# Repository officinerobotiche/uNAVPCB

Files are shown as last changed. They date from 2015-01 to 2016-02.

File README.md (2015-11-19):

# Officine Robotiche &micro;Nav PCB
**The first DC motor board in 4cm X 4cm** - PCB boards for &micro;Nav

This is a project in development by [Officine Robotiche] team, the check info at [official &micro;Nav site](http://unav.officinerobotiche.it/).

Feel free to ask for help, submit suggestions, satisfy your curiosity on our [**Users Group**](https://groups.google.com/forum/?hl=it#!forum/unav-users)

###Join on open firmware project [uNAV.X](https://github.com/officinerobotiche/uNAV.X)!!!

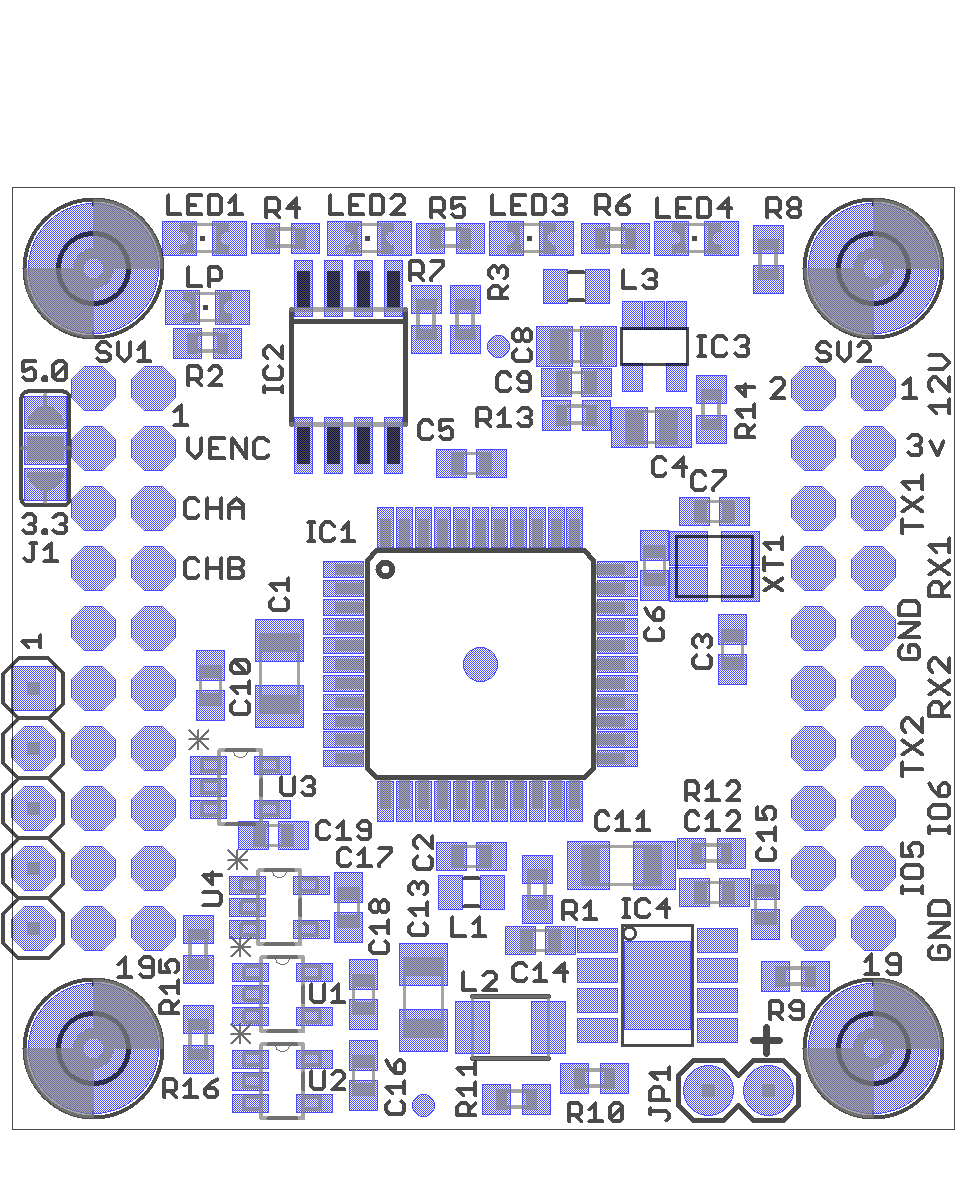
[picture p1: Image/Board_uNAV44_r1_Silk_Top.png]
uNAVPCB Silkscreen Top

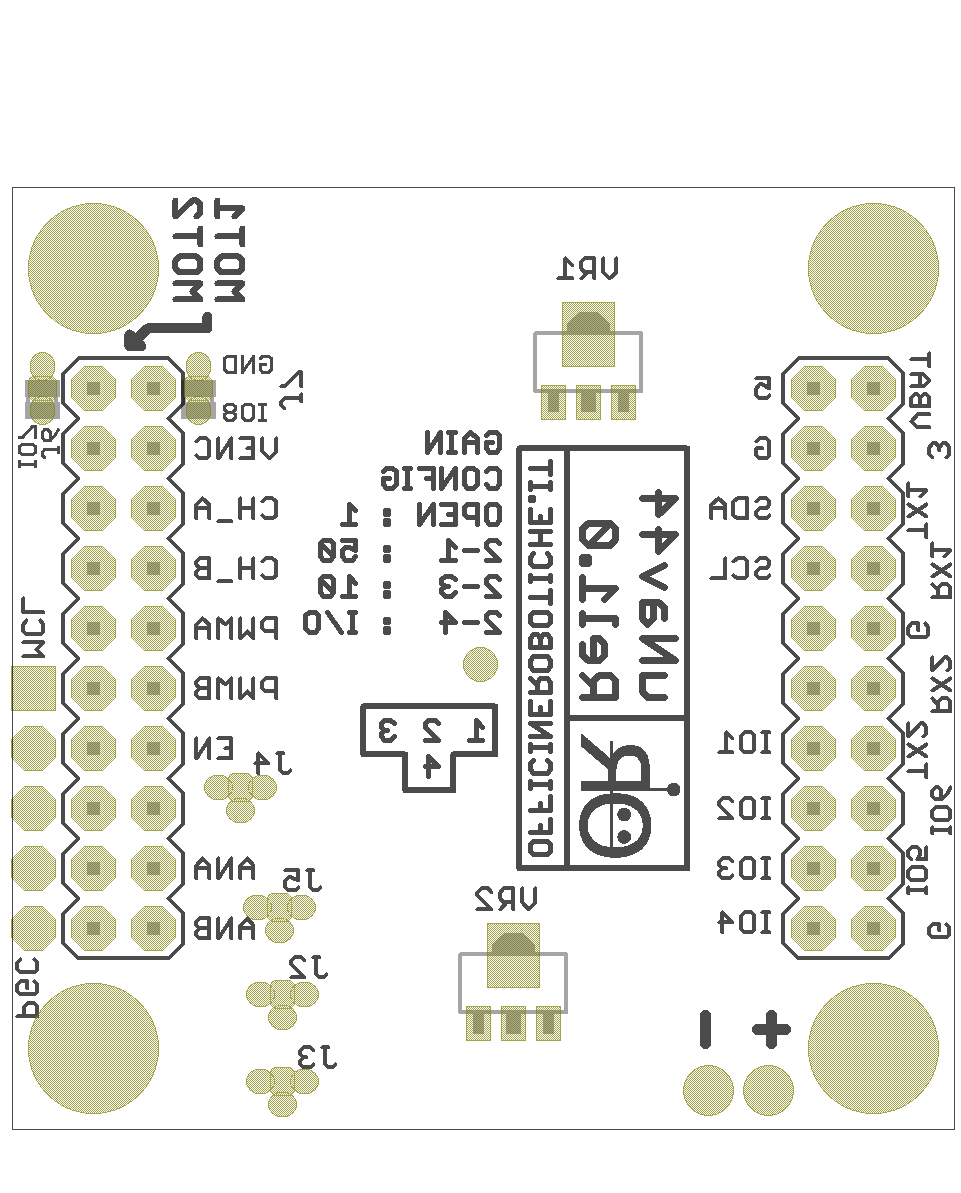
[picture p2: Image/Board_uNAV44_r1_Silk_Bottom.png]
uNAVPCB Silkscreen Bottom

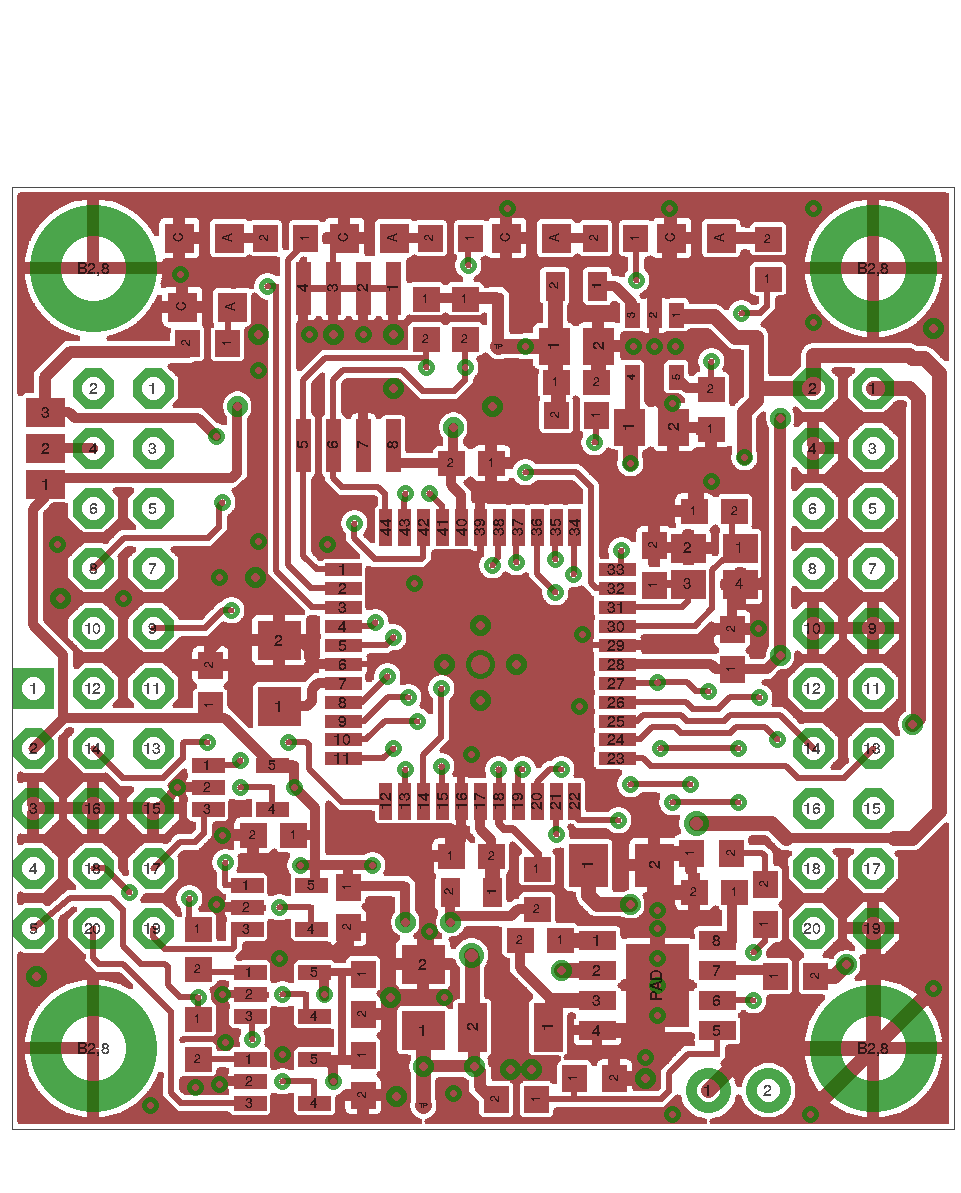
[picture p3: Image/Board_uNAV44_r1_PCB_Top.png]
uNAVPCB Silkscreen PCB Top

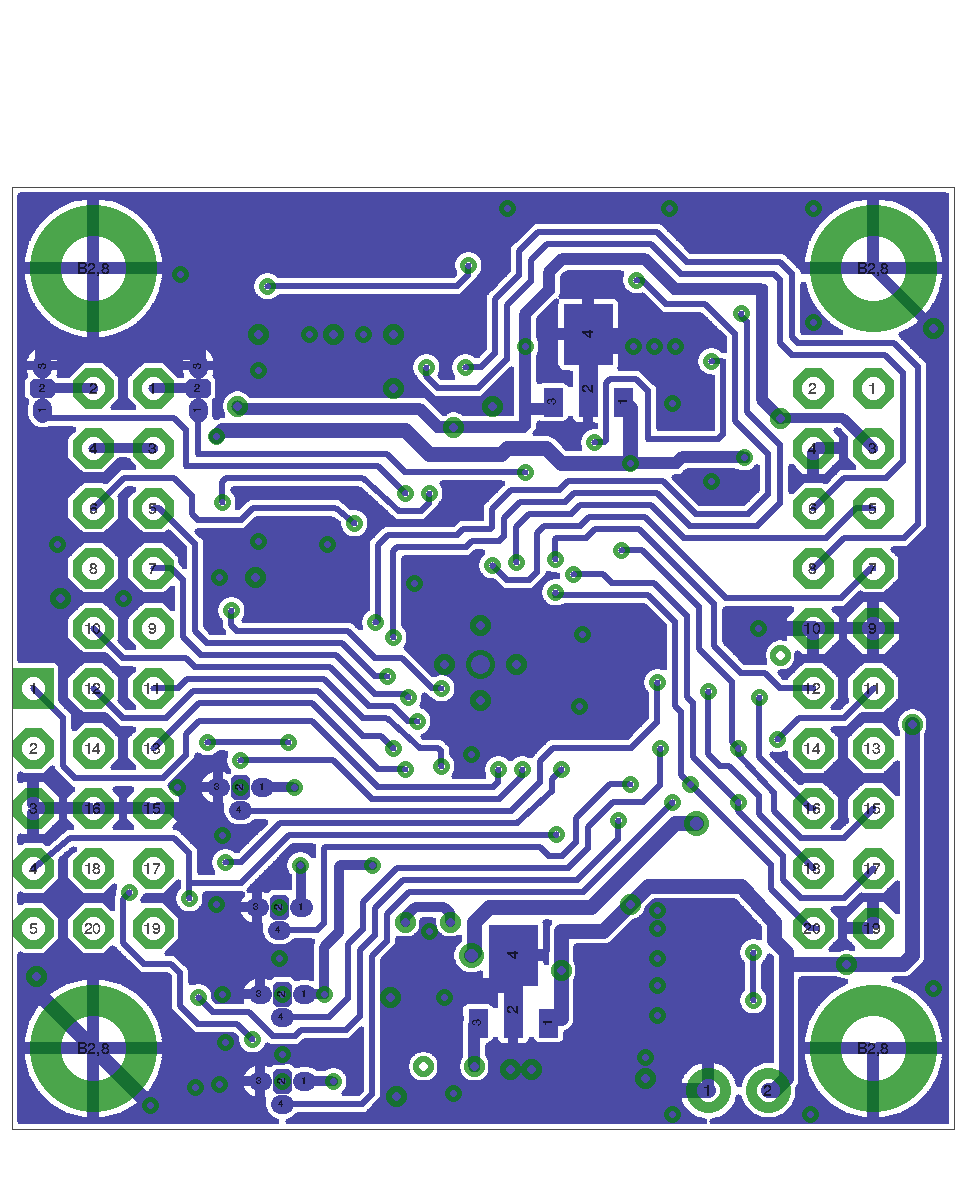
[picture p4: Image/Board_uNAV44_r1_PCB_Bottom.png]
uNAVPCB Silkscreen PCB Bottom


# Hardware features
- 2 DC motor control (external encoders and double H-bridge are required)
- size: 4cm x 4cm
- Matrix board with holes 2.54mm compliant
- Free 256Kb EEPROM in I2C 
- Voltage input *(Max 23V to 6V)*
- 2 internal regulators:
  - External input -> 5V
  - 5V -> 3.3V
- 4 LEDs
- ICSP programming

## DC Motor control
- 2 PWM outputs to control the speed of the motors
- Encoder input. *You can select 5V input or 3.3V to power on your encoders*: 
  - 2 channels (A, B)
  - 3 channels (A, B and Z axis)
- Analog input for current sensing
- Analog input for temperature sensing
- Pin to enable H-Bridge

## Communications
- 2 serial ports
- 1 I2C port
- 7 GP I/O (You can add feature remapping pins) 
 
# Available Shields
- [&micro;Bridge](https://github.com/officinerobotiche/uBridgePCB)

# Graphical tool for PID tuning
- [uNav_PID_Tuner](https://github.com/officinerobotiche/uNav_PID_Tuner)

[Officine Robotiche]:http://www.officinerobotiche.it/
[Logo]:http://2014.officinerobotiche.it/wp-content/uploads/sites/4/2014/09/ORlogoSimpleSmall.png

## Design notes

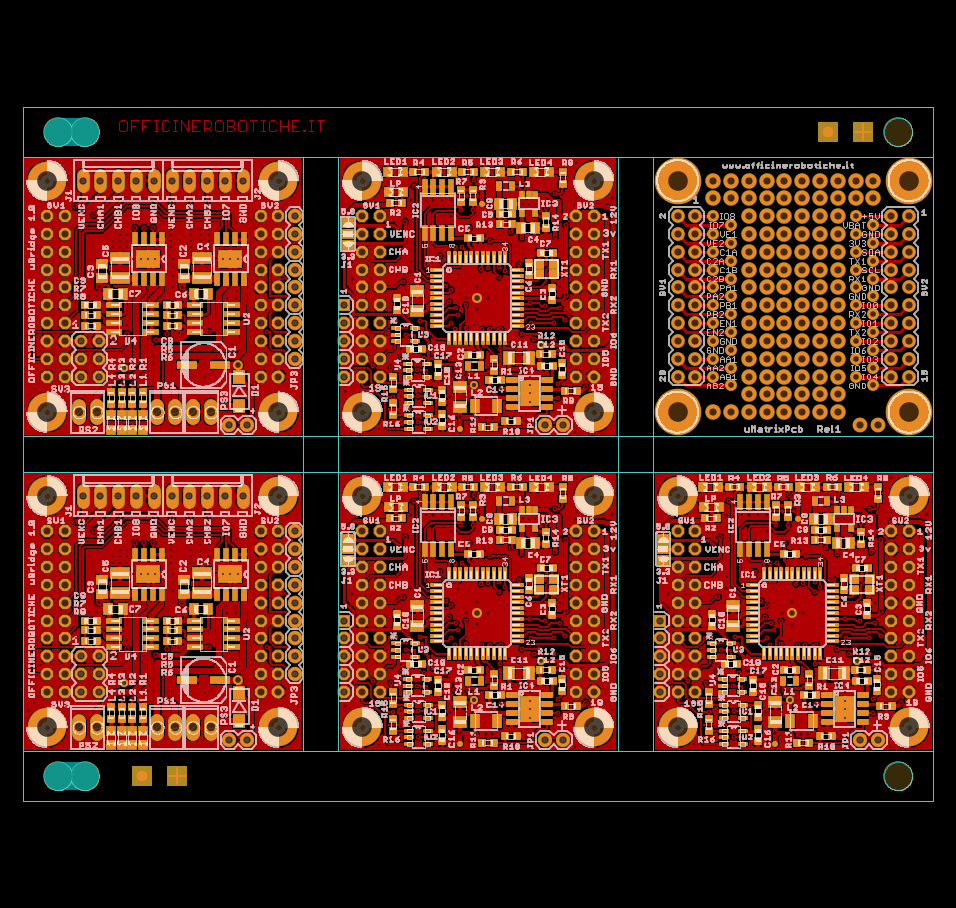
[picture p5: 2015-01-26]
Pannel/Image/Pannel_Top.png

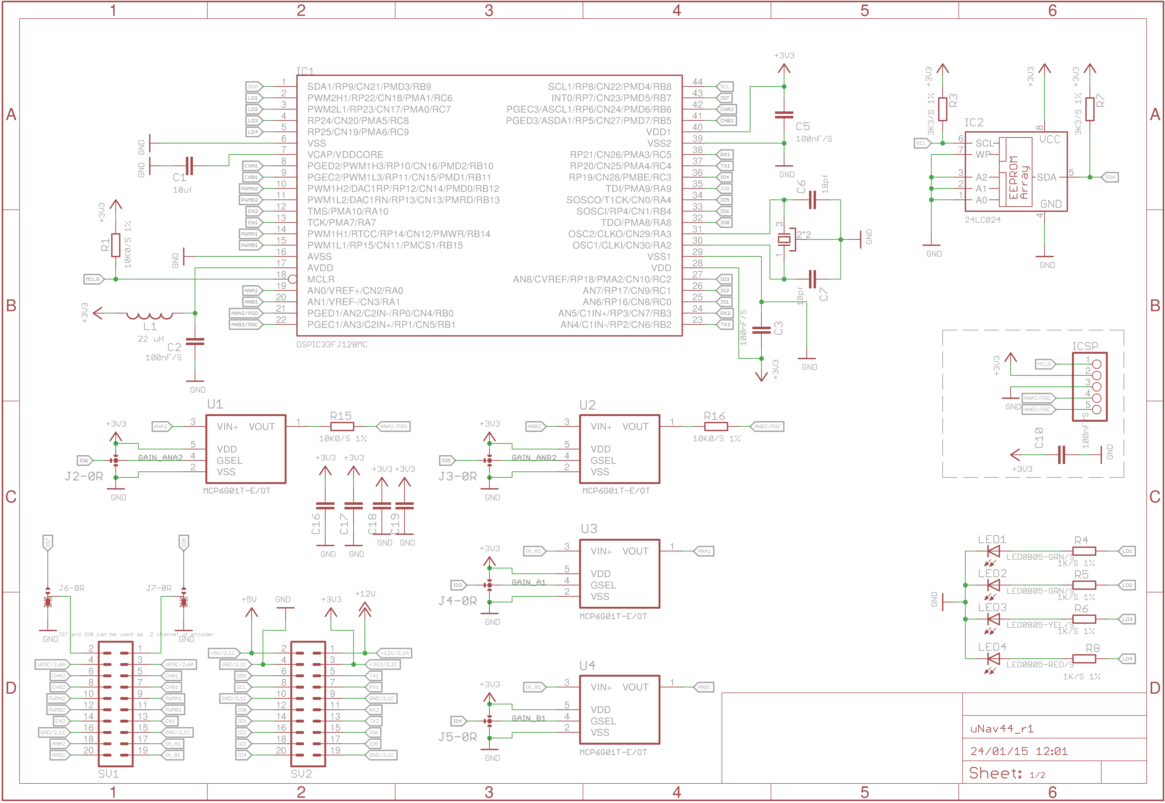
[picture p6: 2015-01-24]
Image/Scheme_uNAV44_r1_Sheet_1.png

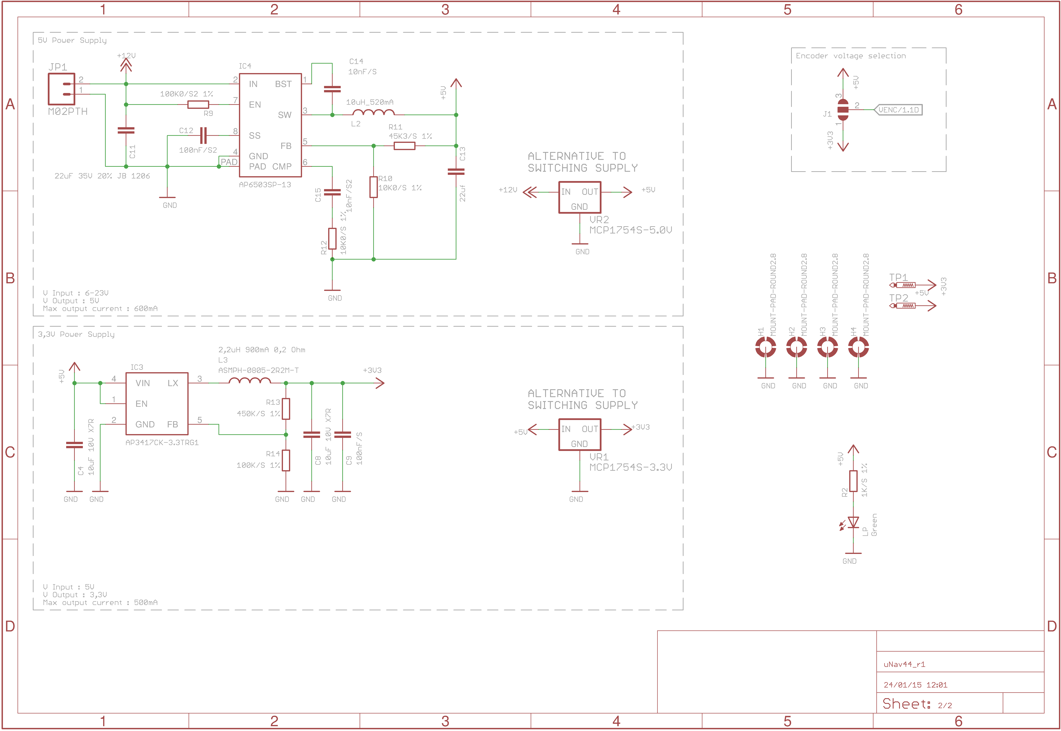
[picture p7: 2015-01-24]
Image/Scheme_uNAV44_r1_Sheet_2.png

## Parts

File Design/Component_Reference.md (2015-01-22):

#3V3 PSU
##AP3417CKTR-G1 : 0,3€
	- http://diodes.com/datasheets/AP3417C.pdf
	- http://www.digikey.it/product-detail/it/AP3417CKTR-G1/AP3417CKTR-G1DICT-ND/4505308
##2,2uH inductor : 0,26€
	-	http://www.abracon.com/Magnetics/power/ASMPH-0805.pdf
	- http://www.digikey.it/product-detail/it/ASMPH-0805-2R2M-T/535-12272-1-ND/4214872
##10uF 10V 20% X7R 0805 : 0,12€
	- http://www.digikey.it/product-detail/it/GRM21BR71A106MA73L/490-10517-1-ND/5026448

#For 6-23V to 5V PSU
##AP6503SP-13
	- http://www.diodes.com/datasheets/AP6503.pdf
	- http://www.digikey.it/product-detail/it/AP6503SP-13/AP6503SP-13DICT-ND/2767830
##22uF capacitor
	- CAP CER 22UF 35V 20% JB 0805 0,89€
	- http://www.digikey.it/product-detail/it/C2012JB1V226M125AC/445-11527-1-ND/3953193
	- CAP CER 22UF 35V 20% JB 1206 0,6€
	- http://www.digikey.it/product-detail/it/C3216JB1V226M160AC/445-11739-1-ND/3953405
##10µH Inductor 520mA/450mA 0806
	- http://www.yuden.co.jp/ut/product/category/inductor/BRC2016T100K.pdf
	- http://www.digikey.it/product-detail/it/BRC2016T100K/587-2177-1-ND/2002875

#Other new used components
##Xtal 10MHZ 8PF SMD: 0,55€
	- http://www.digikey.it/product-detail/it/7V-10.000MAAV-T/887-1791-1-ND/3586039
	- http://www.txccrystal.com/images/pdf/7v.pdf
##MCP6G01T-E/OT Selectable Gain Amplifier: 0,45€
- [DigiKey MCP6G01T-E/OTCT-ND]:http://www.digikey.com/product-detail/en/MCP6G01T-E%2FOT/MCP6G01T-E%2FOTCT-ND/1979730
- [DATASHEET of MCP6G01T-E/OT]:http://ww1.microchip.com/downloads/en/DeviceDoc/22004b.pdf

#Evaluated but discarded
##IC EEPROM 16KBIT 1MHZ SOT23-5 AT24C16D-STUM-T
- [DigiKey AT24C16D-STUM-TCT-ND]:http://www.digikey.it/product-detail/it/AT24C16D-STUM-T/AT24C16D-STUM-TCT-ND/5055821

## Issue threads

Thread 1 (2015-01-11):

Encoder connector in uBridge

rbonghi, 2015-01-11:
I would like to connect encoders in same uBridge board, this is possible?

I told with @Marnic @katodo on the meeting.

Marnic, 2015-01-11:
just added in sch file, @katodo now work on the board

rbonghi, 2015-01-12:
:+1:

katodo, 2015-01-12:
Ok, tomorrow I can check scheme...

katodo, 2015-01-20:
With jumper on I/O7 and I/O8  pin I can use this pin as GND for encoder attached directly on uNAV44.
This issue can be reopened on uBridge Repo.

Closed 2015-01-20.

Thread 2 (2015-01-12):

5 volt voltage regulator on board, why not?

bobboteck, 2015-01-12:
I saw that you have removed the 5Volt voltage regulator, this is not a choice that I like. Personally, I usually use a switching regulator Output 6.5 / 7.0V, this voltage reaches the various boards, where each has its voltage regulator for the required voltage. This, in my view, be also another benefit with regard to the cleaning of the supply signal, a cable that carries the 5V around for the robot is more subject to noise, and if used for direclty power a board, it can create problems.

Myzhar, 2015-01-12:
If you think to use the regulated 5V to power external encoders without the necessity to use other boards, I agree with you and I say that the uNav must have a 5V regulator onboard that generates that power voltage.

The only thing that makes me thinking is the power dissipation. Do we have enough space to place a power dissipator for the linear regulator?

@katodo @rbonghi @Marnic @guiott

katodo, 2015-01-12:
Have you statistic about encoder power consumption? there are a lot of
encoder type....
Can you also measure power supply current of uNav with software running?

Mauro Soligo by Sony Xperia Z
Il 12/gen/2015 16:32 "Walter Lucetti" <notifications@github.com> ha scritto:

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

katodo, 2015-01-12:
Ok, I've analyzed the problem and 5V are required! :)

Now, I can keep old solution with 2 LDO but I've found some better solution:
- http://www.analog.com/static/imported-files/data_sheets/ADP1864.pdf
- http://www.torex.co.jp/english/products/dcdc_converters/data/XC9503.pdf

First code can be powered with a supply up to 14V, second IC is dual-output and can be used for 3,3/5V out with a supply from 6 to 10V
They are a more expensive solution ( about 2€ Vs. <1€ of LDO version ) but is a very efficiency....

rbonghi, 2015-01-13:
I think second IC is more convenient to save space on PCB board and we don't use second layer to put ICs.

Finally I think is important to put a 5V regulator to power (in stand-alone version) the encoders.

katodo, 2015-01-13:
Price is 1,3€/each for 100pcs on digikey, with inductor and external mosfet solution can be expensive... now I search another IC...

katodo, 2015-01-13:
Another idea, a 2-stage supply:
Vin -> 5V with:
http://www.digikey.it/product-detail/it/AP6503SP-13/AP6503SP-13DICT-ND/2767830
Less than 0,7€ and up to 23V input

5V -> 3,3V with:
http://diodes.com/datasheets/AP3417C.pdf
http://www.digikey.it/product-detail/it/AP3417CKTR-G1/AP3417CKTR-G1DICT-ND/4505308
Less than 0,3€, without diode ( SYNCHRONOUS ) with a 2,2uH inductor ( @ 1,5Mhz ), can be the perfect solution for 3,3Vout in a space-save idea...

This is a complex but professional solution and no extremely expensive... with inductor and capacitor we are below 2,5€

@katodo @rbonghi @Marnic @guiott @bobboteck can be ok?

rbonghi, 2015-01-13:
ok! :+1:

bobboteck, 2015-01-13:
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

If there is enough space, for me is OK!!!

Marnic, 2015-01-13:
OK

katodo, 2015-01-20:
In final revision of scheme there are 2-stage switching reglator and optional LDO regulator... I consider closed this issue.

Closed 2015-01-20.

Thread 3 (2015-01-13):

Analog input analisys

katodo, 2015-01-13:
In uNav board there are 4 inputs reserved for analog operation.

In my idea all input must be "general porpouse" with a 0-3,3V input range and a medium high input impedance.

I've remove OA in board because pic input is also a "semi-general-porpouse" input and Operational Amplifier-related section is very conditioned by type of measure:

Measure of current in L'298 like shunt resistor require a gain depending by current and shunt resistor. For example with 2A on 0,1 Ohm resistor I need a gain of 16,5 to obtain 0-3,3 V range, but with a different driver driver like Allegro A4950 I need a 3,7 gain ( 3,5A and 0,25 Ohm resistor )... In this case OA section is not required and is only redundant.
In other bridge with hall-effect current sensor IC there are +/-5A +/-10A or bigger full-scale ( 2,5V @ 0A measure ) and a programmable OA can be required for a big accuracy on low current measure.
Also, a filter can be required...

Input for Voltage measure require a different section, I need a voltage divider and a filter depending by type of measured voltage ( input voltage, motor coil voltage etc... )

Besides, measure conditioning mus be near source of current/voltage under test... and in all case input section can't be equal and fixed...

guiott, 2015-01-13:
In the dsNav version of motor controller (see attached) there is an amplifier with a gain of 1 or 10 selectable by a soldering jumper. That's enough for a L298 h-bridge too, as I've used on Rino. Furthermore there is a minimal low-pass filter to filter out the PWM frequency. Further filtering is achieved via software procedures: using DMA of dsPIC33F ADC you can get 16 samples with no CPU intervention and compute the average after the interrupt trigger.
I agree at all that this can be redundant in many cases and the best solution is to condition the signal where it's generated, but this keep the board more general purpose.

On the other hand a simpler board, with less components, placed on the top layer only, costs less and results more attractive to most of the possible customers.

Is it possible to calculate the cost saving in the simpler solution? I think this is the best parameter to discuss on.

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

___________________
http://www.guiott.com/

katodo, 2015-01-13:
Ok, I'm evaluating this IC:
http://ww1.microchip.com/downloads/en/DeviceDoc/22004b.pdf
http://it.farnell.com/microchip/mcp6g01t-e-ot/amp-select-gain-single-1-mhz-smd/dp/1332148?ost=1332148

Gain is pin-selectable from 1, 10 and 50 value, IC is Rail-ToR-Rail and supplies is 1,8-5V range...
IC is small but I suspect that bottom side wil be needed and filer can't be perfomed in HW...
Voltage supply can be the same of dsPIC... ad will be the same...

During PCB update I will choose ideal version of IC ( 4pcs 1-channel or 1 IC at 4 ch ).
About 2 side version cost's, there are a lot of thing to be evaluated but in this stage I consider that, if there are some  IC on bottom side of PCB, they can be hand soldered.

@guiott @Marnic @Myzhar @rbonghi @bobboteck  can you "vote" this possible solution ( +1 or -1 )?

guiott, 2015-01-13:
Like!

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

___________________
http://www.guiott.com/ <http://www.guiott.com/>

Marnic, 2015-01-13:
OK
1++

Da: "Katodo" notifications@github.com
A: "officinerobotiche/uNAVPCB" uNAVPCB@noreply.github.com
Cc: "Marnic" marco@fabbrimarco.com
Data: Tue, 13 Jan 2015 01:14:45 -0800
Oggetto: Re: [uNAVPCB] Analog input analisys (#3)

> Ok, I'm evaluating this IC:

> http://ww1.microchip.com/downloads/en/DeviceDoc/22004b.pdf

> http://it.farnell.com/microchip/mcp6g01t-e-ot/amp-select-gain-single-1-mhz-smd/dp/1332148?ost=1332148

> Gain is pin-selectable from 1, 10 and 50 value, IC is Rail-ToR-Rail and supplies is 1,8-5V range...
>
IC is small but I suspect that bottom side wil be needed and filer can't be perfomed in HW...
>
Voltage supply can be the same of dsPIC... ad will be the same...

> During PCB update I will choose ideal version of IC ( 4pcs 1-channel or 1 IC at 4 ch ).
>
About 2 side version cost's, there are a lot of thing to be evaluated but in this stage I consider that, if there are some  IC on bottom side of PCB, they can be hand soldered.

> @guiott @Marnic @Myzhar @rbonghi @bobboteck  can you "vote" this possible solution ( +1 or -1 )?

> —
> Reply to this email directly or view it on GitHub.
>
  >

rbonghi, 2015-01-13:
:+1:

bobboteck, 2015-01-13:
+1

Myzhar, 2015-01-14:
+1

2015-01-13 16:28 GMT+01:00 Bobboteck <notifications@github.com>:

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

--
*Walter "Myzhar" Lucetti*

email myzhar@robot-home.it
web: *www.robot-home.it <http://www.robot-home.it/> - www.opencv.it
<http://www.opencv.it/>*
project:  http://myzharbot.robot-home.it

katodo, 2015-01-20:
in final revison of scheme I've added OA with configurable GAIN using MCU I/O... I consider closed this issue

Closed 2015-01-20.

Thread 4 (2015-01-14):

Component exchange for miniaturization

katodo, 2015-01-14:
can be exchanged this component?
- Actual 24AA01 EEPROM with this  AT24C16D-STUM-T 16Kbit in SOT23 case?
  http://www.digikey.it/product-detail/it/AT24C16D-STUM-T/AT24C16D-STUM-TCT-ND/5055821

- Actual 10Mhz xtal with this:
  http://www.digikey.it/product-detail/it/NX5032GA-10.000000MHZ-LN-CD-1/644-1033-1-ND/1128905

@rbonghi @guiott @Cyb3rn0id @Marnic @bobboteck

bobboteck, 2015-01-15:
I think there is no problem, you can talk to @guiott that developed the code to control the eeprom

katodo, 2015-01-15:
EEprom is last IC that can be changed but is a possibility.

Cordiali saluti
                        Mauro Soligo

Katodo  di Mauro Soligo
Via Molino Nuovo, 31 35012 Camposampiero PD Italy
P.IVA 04161520285  C.F. SLGMRA80L18B563Y
Cell: +39 3462137146  FAX: +39 0498591588  e-mail mauro.soligo@katodo.com

2015-01-15 12:16 GMT+01:00 Bobboteck <notifications@github.com>:

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

rbonghi, 2015-01-15:
I'm agree to increase free area space on unav pcb board. :+1:

katodo, 2015-01-19:
Only XTAL was changed.

Closed 2015-01-19.

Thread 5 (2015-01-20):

Move GND near TX2

bobboteck, 2015-01-20:
Is possible in the BUS connector, move the actual GND near IO5, near the TX2 pin, in place oh IO6?

Marnic, 2015-01-20:
you think to use two UART? if not, you can make just only one cable TX-RX-GND and if you rotate the cable 180 degrees you have GND-RX-TX so as displaced in the bus connector

katodo, 2015-01-20:
and, if you use 2 uart, you can use a single cable with a common GND...

Replace a I/O with GND isn't possible in this board, I'm sorry.

  Mauro

2015-01-20 11:06 GMT+01:00 Marnic <notifications@github.com>:

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

bobboteck, 2015-01-20:
@Marnic, Yes use two UART, if you want connect two uNav!

Ok if is not possible, as I said it's only a question "if is possible".

Closed 2015-01-20.

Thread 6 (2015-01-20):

Fourth mount pad

bobboteck, 2015-01-20:
I have see there is only 3 mount pad, but we have four hole. I see also there aren't enough sapce to put it. My question is, tis hole can't be used for mounting the board?

katodo, 2015-01-20:
3 pad have GND ring and fourth PAD is a simple hole, can be used for PCB fix but must be used with caution ( plastic screw or washer ). In final version I can check a solution...

katodo, 2015-01-22:
Added... solved :)

Closed 2015-01-22.

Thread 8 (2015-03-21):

Inversion of polarity destroy uNav

katodo, 2015-03-21:
uNav used without uBridge will be destroyed is inversion supply voltage occur.

A input diode can be usefull...

Myzhar, 2015-03-23:
Yeah! Protection anti-inversion is useful...
Il 21/Mar/2015 02:09 "Katodo" <notifications@github.com> ha scritto:

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

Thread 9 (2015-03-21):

Input inductor size

katodo, 2015-03-21:
A 15uH 1,2A 0.204 Ω in 4,5x4mm size is better inductor in input switching power supply.
In V1 PCB version can be soldered but in V2 pcb module bust be updated.

Ideal component is Wurth Elektronik code:  744773115

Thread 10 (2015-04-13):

C16 to C19 Capacitor size

gbr1, 2015-04-13:
C16 C17 C18 C19 capacitors size isn't specified

Myzhar, 2015-04-13:
The capacitors are 100nF

@katodo please add the information on the schematic as soon as you can

katodo, 2015-04-13:
ok, information in SCH file is hidden only  ( in 1.1.sch file). If you open file with Eagle vale can be read, in next days I try to update file on Git.

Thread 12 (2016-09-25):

Change PGED & PGEC lines

rbonghi, 2016-09-25:
At this time the PGED & PGEC lines are connected on pin 21 and 22. The same line of motor 1 current and voltage adc line.

I suggest to move in other place. In  PGED3 & PGEC3, in pin 41, 42 and move CHB1 and CHB2 in other remappable place.

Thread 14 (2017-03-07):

Discussion of board

Russ76, 2017-03-07:
Do you have somewhere posted a comprehensive discussion of what you are trying to accomplish with this project, and how this board(s) will be superior to other alternatives already on the market? Will it control large motors, like 25 amps? Is the ROS software available now for use of this board?

Myzhar, 2017-03-07:
@Russ76 you are putting good questions.

We are still trying to understand if "reinventing the wheel" is a good road to follow.

The starting idea was the one to create by ourself a tiny dual channels motor driver (4cm x 4cm)  with logic and power separated. This module (uNAVPCB) cannot directly drive any motor because it only generates two PWM signals to be sent to an external H-Bridge, controlling speed (dual channels QEI encoders are supported) and torque, if you can provide analog current sensing.

I can reply to the second of your question: YES, you can drive large motors, only if you use the right H-Bridge for that kind of motors. The uNAV can theoretically drive any kind of motor...

About ROS... yes, we have ROS drivers:  https://github.com/officinerobotiche/ros_orbus_interface
Here you can find the also the firmware for the board: https://github.com/officinerobotiche/uNAV.X

Now the reply to the first question... it is a phylosophical question because analizing the market I can say that there is not the needing for a new motor controller board. You can find a lot of good motor drivers on the market, with a good ROS support, RoboteQ's (e.g. SDC2160) and Ion Motion Control's (RoboClaws) are good examples. Sometimes the market must not be a limitation, a new project can also be a good way to make practice with hardware and to study new software algorithms.
To finish this long reply: if I need to go on the market with a new "robot" I will not create a new motor controller board, but I will use something available off the shelf to not waste time and money; if I want to make a bit of research in the field of motor control I will create my own board trying to understand what I can do better than other product on the market (i.e. speed and torque control on a dual PID loop).

I hope to have replied to all of your question, please let me know what you think about.

Walter

Russ76, 2017-03-07:
Thanks for that, Walter! Your board is very small, that is good. And I'm sure the research and project operation was educational for several of you. Building a robot at this time is an educational project and not easy; there is so much to learn. Just learning ROS itself is challenging.
For motor control I'm using a Sabertooth and Kangaroo. Just installed encoders last week. We'll see how it works. Please let us know when your uNav is market ready!

Myzhar, 2017-03-07:
@Russ76 Thank you

Closed 2017-03-16.

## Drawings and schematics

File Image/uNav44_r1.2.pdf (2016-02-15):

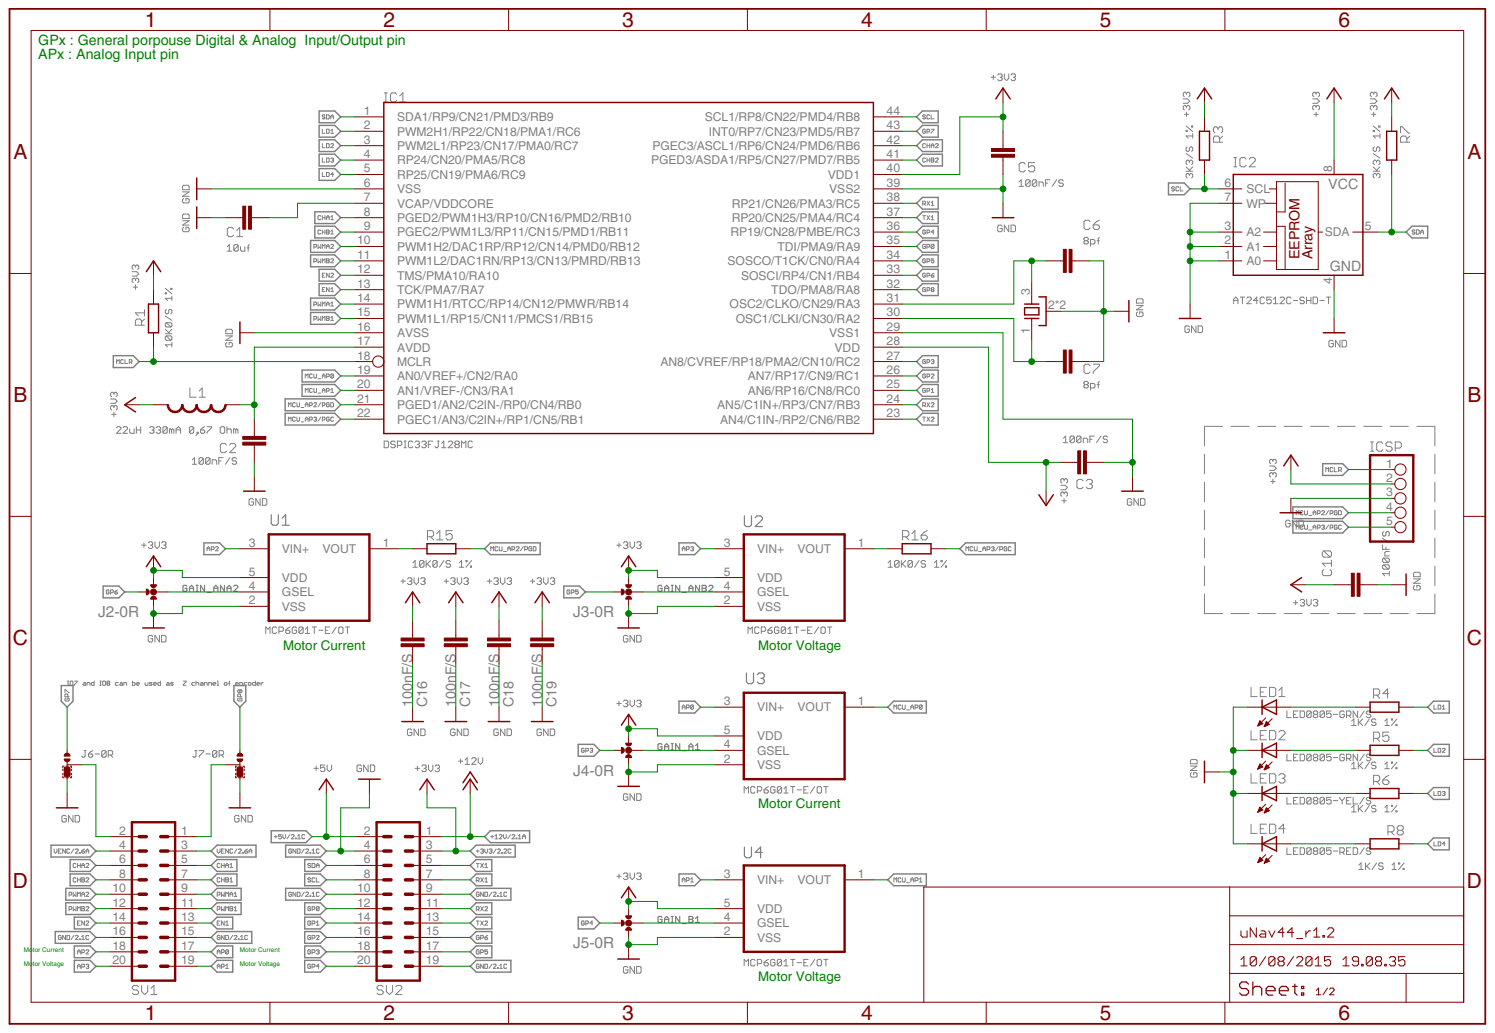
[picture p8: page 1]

100nF/S 100nF/S 100nF/S 100nF/S SDA1/RP9/CN21/PMD3/RB9 1 PWM2H1/RP22/CN18/PMA1/RC6 2 PWM2L1/RP23/CN17/PMA0/RC7 3 RP24/CN20/PMA5/RC8 4 RP25/CN19/PMA6/RC9 5 VSS 6 VCAP/VDDCORE 7 PGED2/PWM1H3/RP10/CN16/PMD2/RB10 8 PGEC2/PWM1L3/RP11/CN15/PMD1/RB11 9 PWM1H2/DAC1RP/RP12/CN14/PMD0/RB12 10 PWM1L2/DAC1RN/RP13/CN13/PMRD/RB13 11 TMS/PMA10/RA10 12 TCK/PMA7/RA7 13 PWM1H1/RTCC/RP14/CN12/PMWR/RB14 14 PWM1L1/RP15/CN11/PMCS1/RB15 15 AVSS 16 AVDD 17 MCLR 18 AN0/VREF+/CN2/RA0 19 AN1/VREF-/CN3/RA1 20 PGED1/AN2/C2IN-/RP0/CN4/RB0 21 PGEC1/AN3/C2IN+/RP1/CN5/RB1 22 AN4/C1IN-/RP2/CN6/RB2 23 AN5/C1IN+/RP3/CN7/RB3 24 AN6/RP16/CN8/RC0 25 AN7/RP17/CN9/RC1 26 AN8/CVREF/RP18/PMA2/CN10/RC2 27 VDD 28 VSS1 29 OSC1/CLKI/CN30/RA2 30 OSC2/CLKO/CN29/RA3 31 TDO/PMA8/RA8 32 SOSCI/RP4/CN1/RB4 33 SOSCO/T1CK/CN0/RA4 34 TDI/PMA9/RA9 35 RP19/CN28/PMBE/RC3 36 RP20/CN25/PMA4/RC4 37 RP21/CN26/PMA3/RC5 38 VSS2 39 VDD1 40 PGED3/ASDA1/RP5/CN27/PMD7/RB5 41 PGEC3/ASCL1/RP6/CN24/PMD6/RB6 42 INT0/RP7/CN23/PMD5/RB7 43 SCL1/RP8/CN22/PMD4/RB8 44 VCC GND 8 4 SCL 6 SDA 5 A0 1 A1 2 A2 3 WP 7 12345 135 246 79 810 111315 121416 1719 1820 135 246 79 810 111315 121416 1719 1820 1 3 2*2 C16 VIN+ 3 GSEL 4 VSS 2 VDD 5 VOUT 1 C17 VIN+ 3 GSEL 4 VSS 2 VDD 5 VOUT 1 VIN+ 3 GSEL 4 VSS 2 VDD 5 VOUT 1 VIN+ 3 GSEL 4 VSS 2 VDD 5 VOUT 1 C18 C19 J2-0R J3-0R J4-0R J5-0R ABCD 1 2 3 4 5 6 ABCD 1 2 3 4 5 6 Array EEPROM GPx : General porpouse Digital & Analog Input/Output pin APx : Analog Input pin Motor Current Motor Current Motor Voltage Motor Voltage Motor Voltage Motor Current Motor Voltage Motor Current

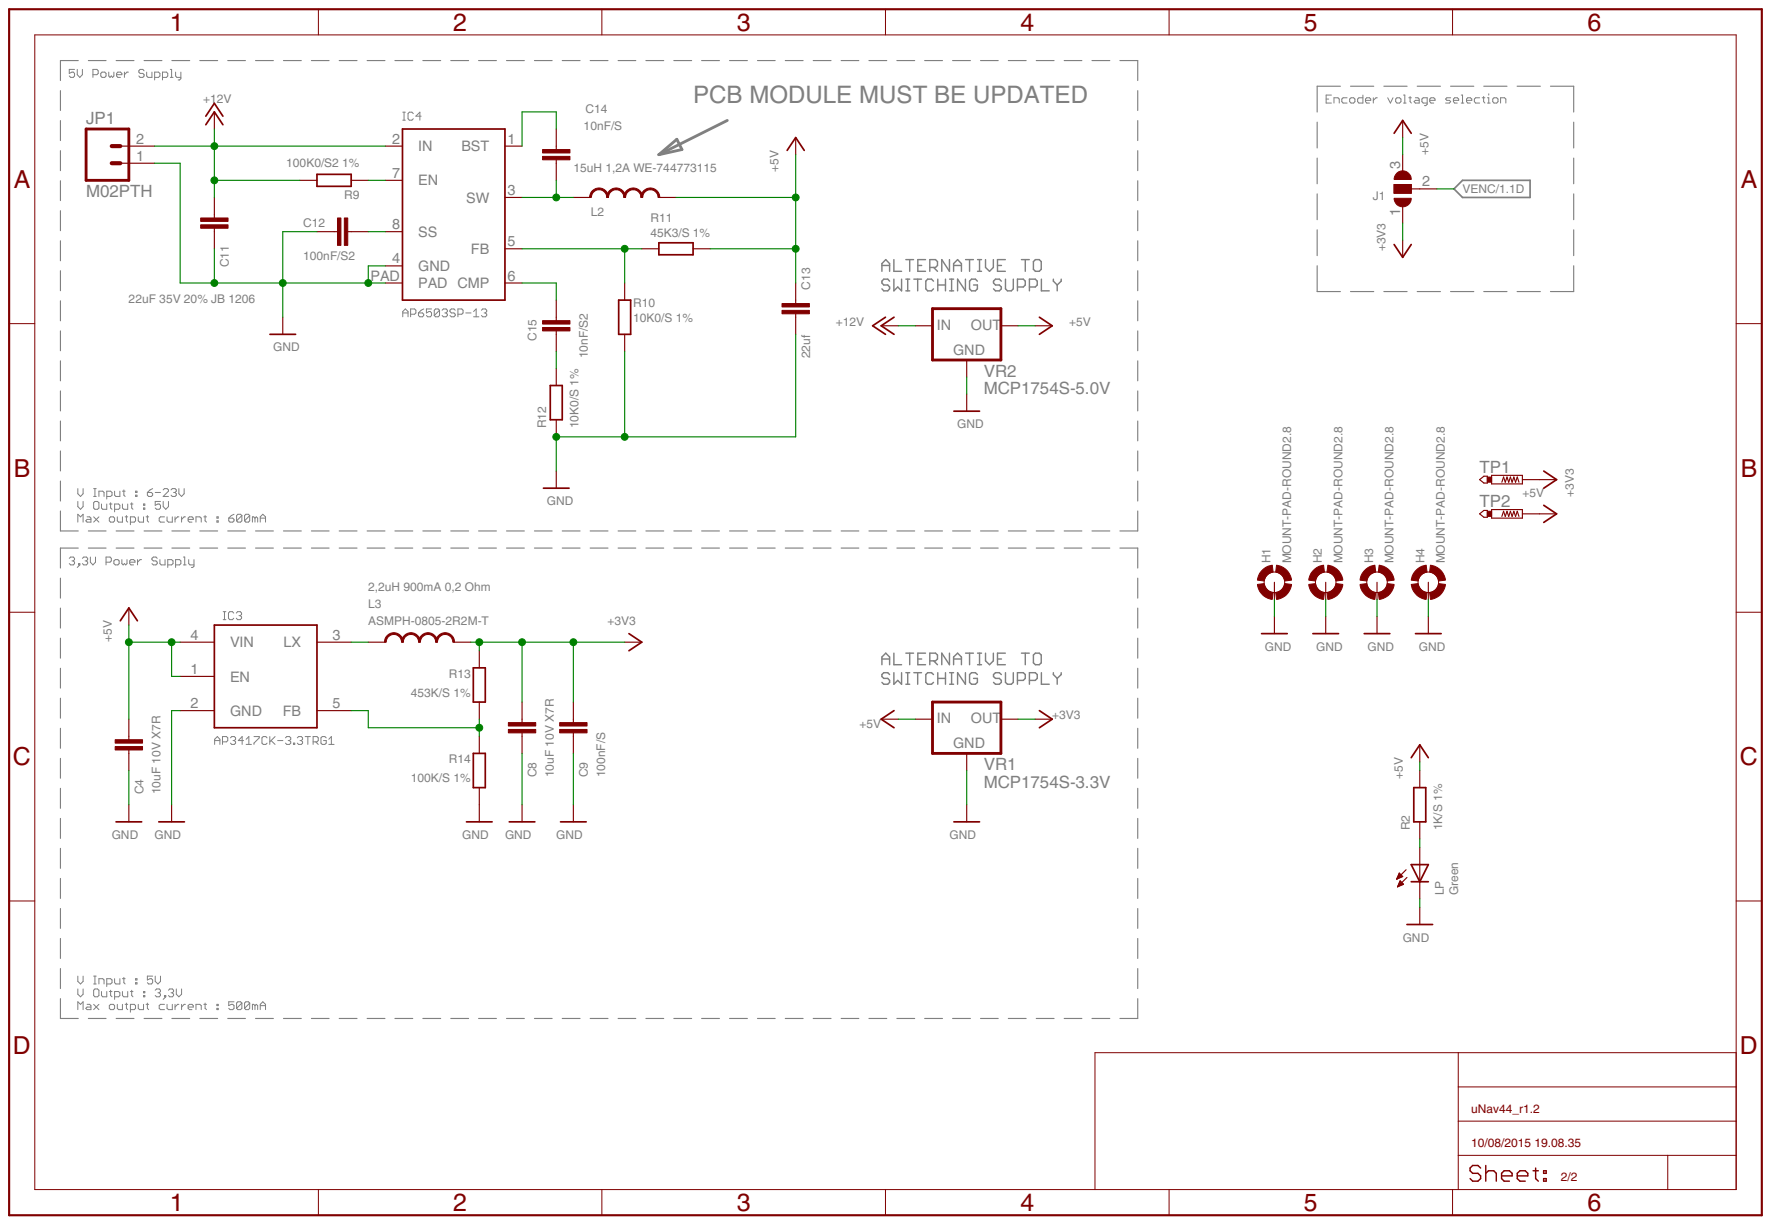
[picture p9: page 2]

PCB MODULE MUST BE UPDATED

MOUNT-PAD-ROUND2.8 MOUNT-PAD-ROUND2.8 MOUNT-PAD-ROUND2.8

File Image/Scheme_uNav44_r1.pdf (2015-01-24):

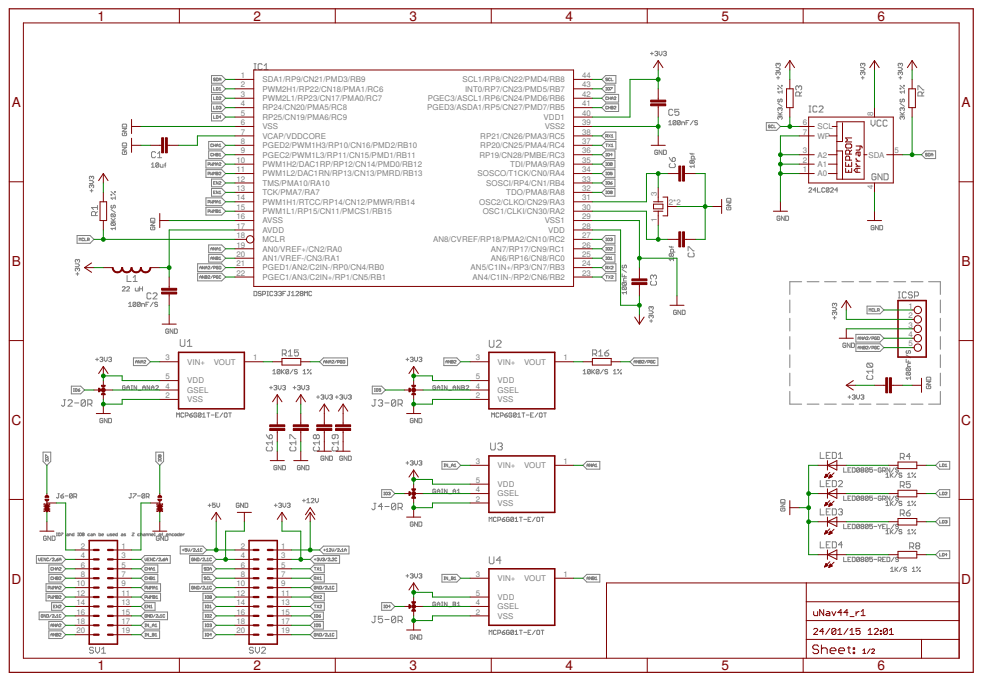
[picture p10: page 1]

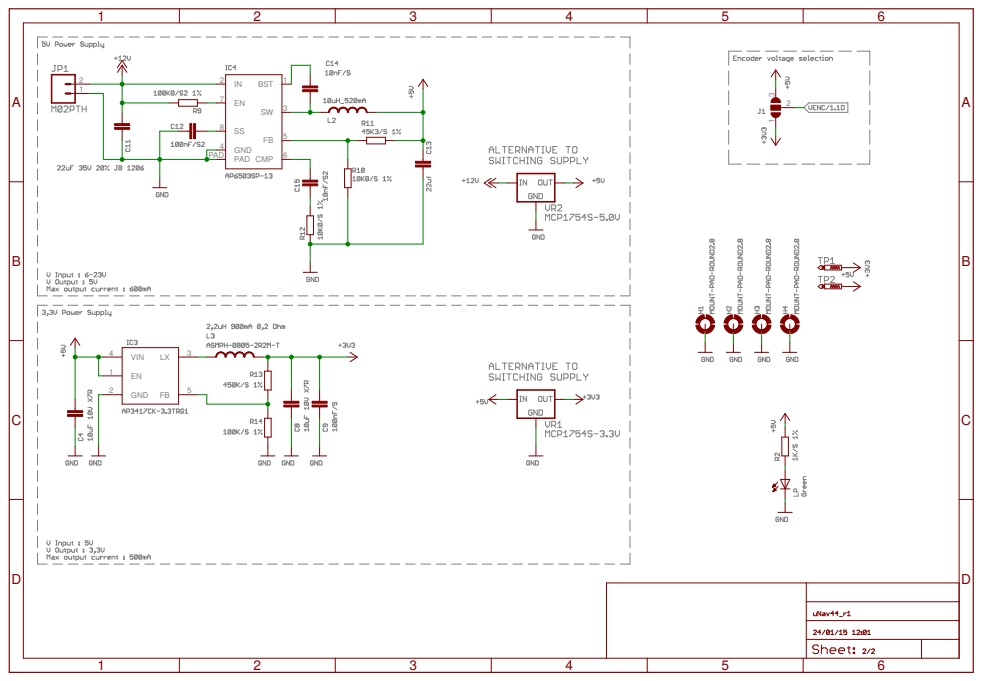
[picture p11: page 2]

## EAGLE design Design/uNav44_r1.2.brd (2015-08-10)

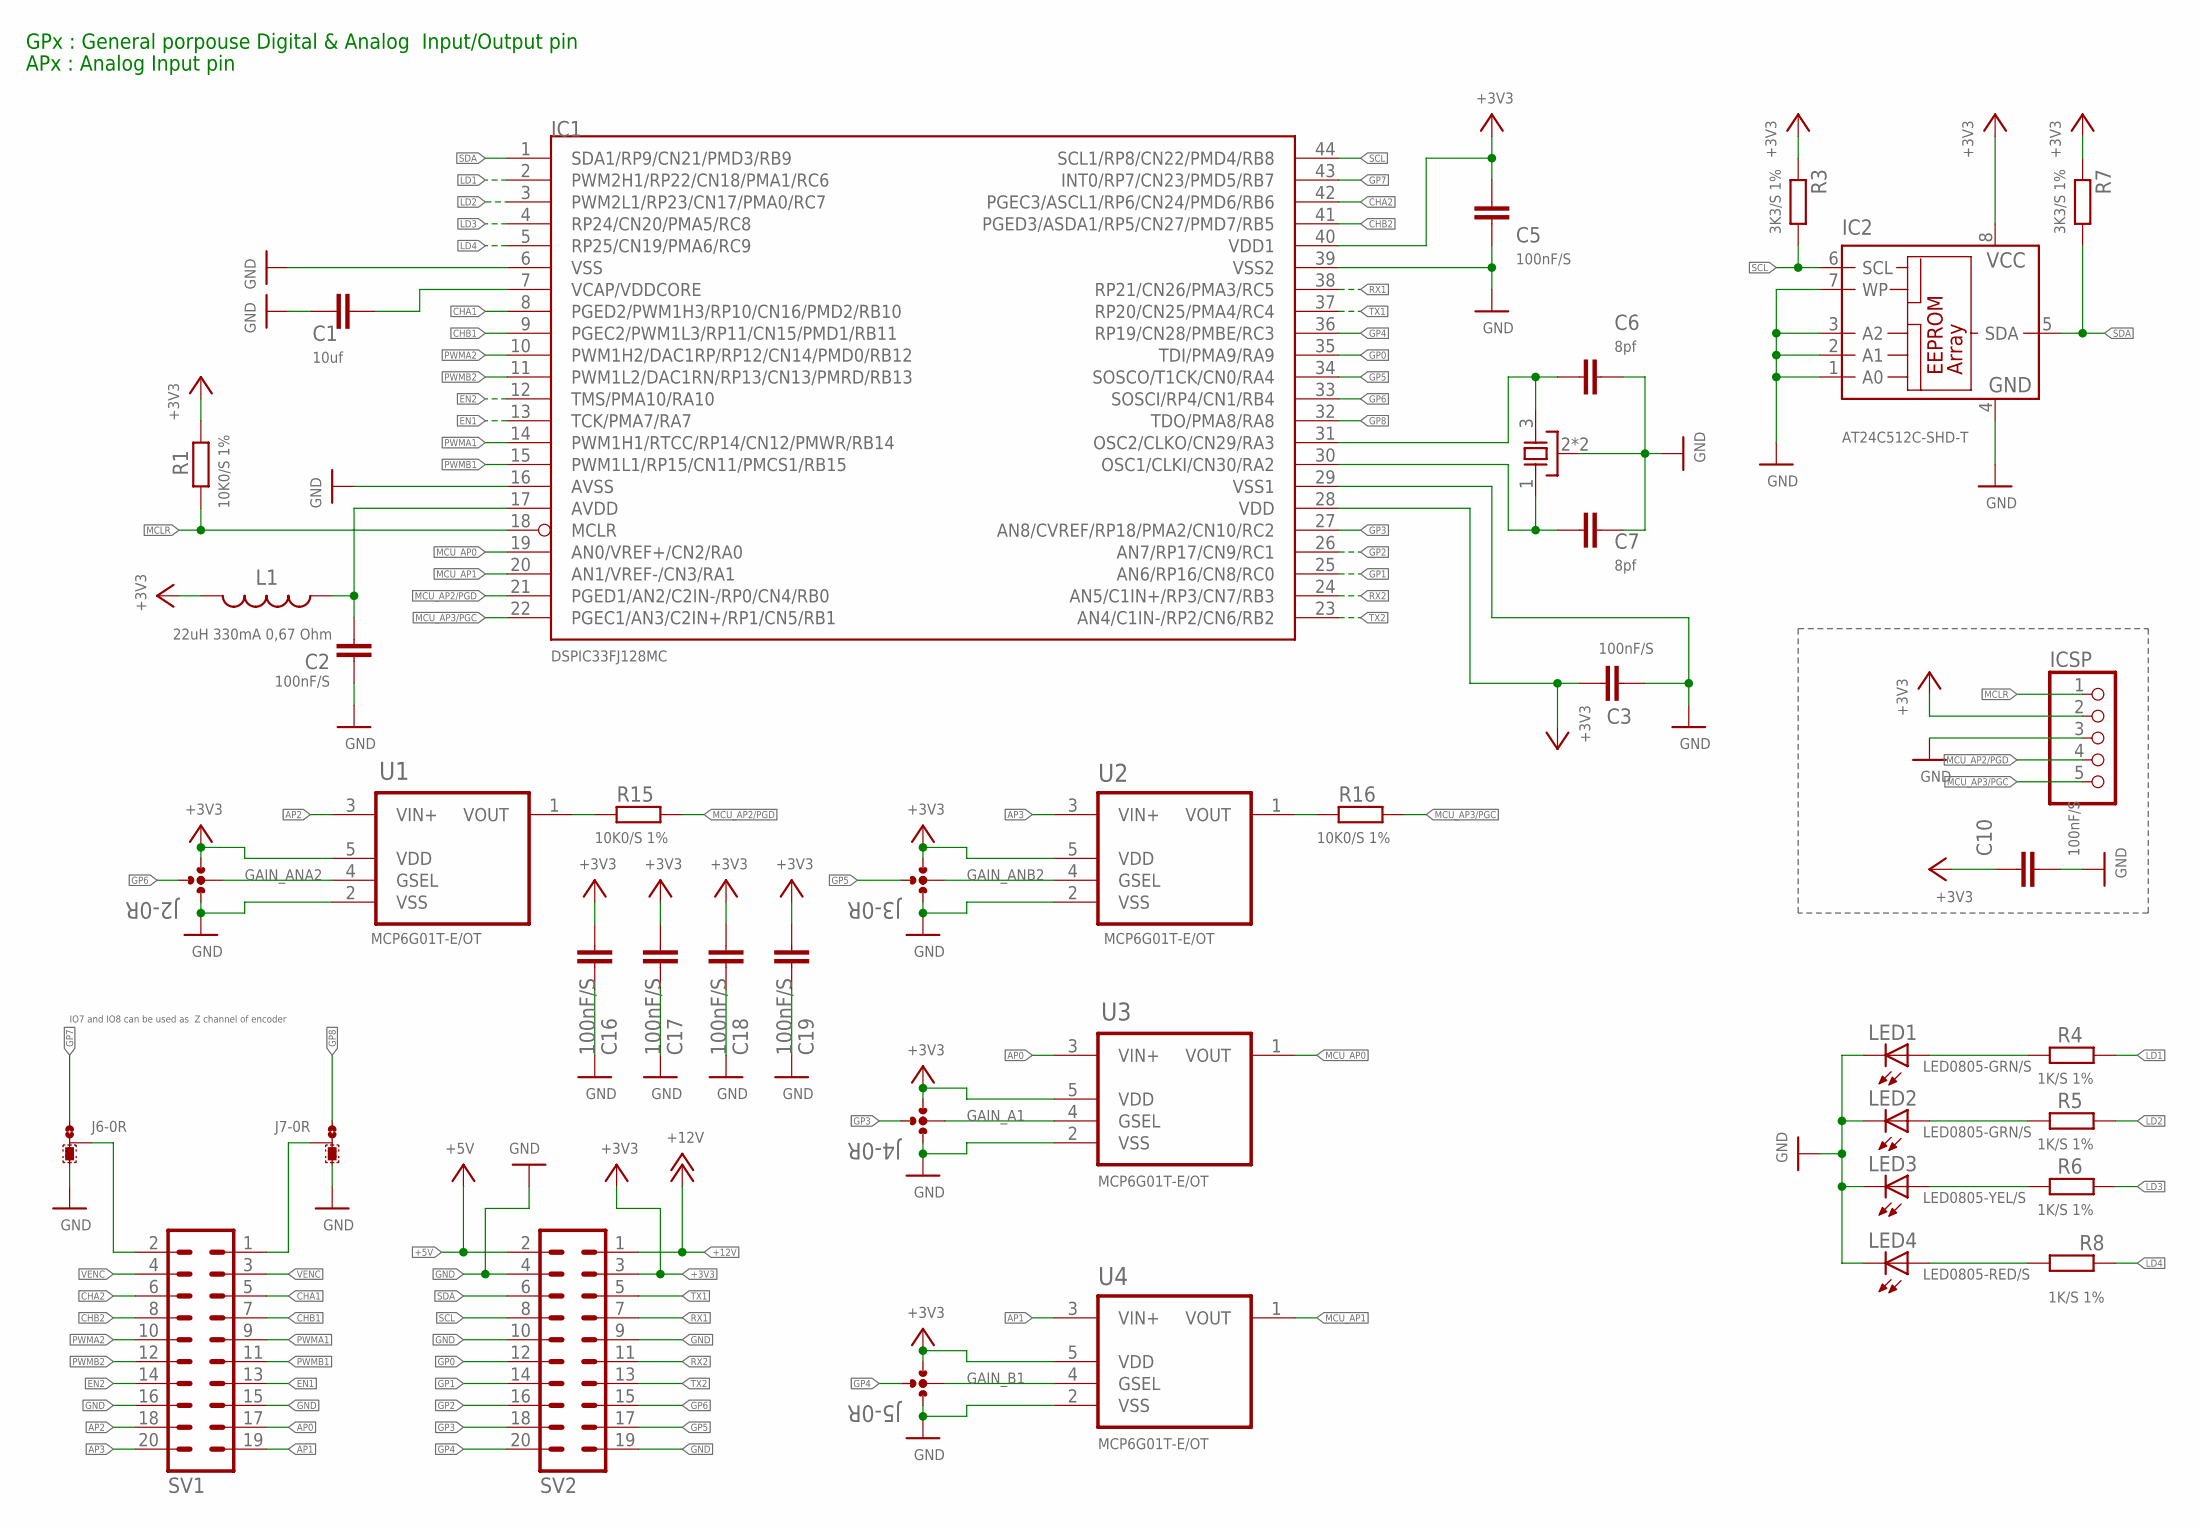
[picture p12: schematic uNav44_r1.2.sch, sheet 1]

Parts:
C1: 10uf; C1206
C2, C3, C5, C10, C16, C17, C18, C19: 100nF/S; C0603
C6, C7: 8pf; C0603
IC1: DSPIC33FJ128MC; TQFP44
IC2: AT24C512C-SHD-T; SO-08M
ICSP: PINHD-1X05_2.54-S; 1X05-S
J2, J3, J4, J5: 0R-JUMP-4; C0R-JUMP-4
J6, J7: 0R-JUMPC; C0R-JMP
L1: 22uH 330mA 0,67 Ohm; 0805
LED1, LED2: LED0805-GRN/S; CHIPLED_0805
LED3: LED0805-YEL/S; CHIPLED_0805
LED4: LED0805-RED/S; CHIPLED_0805
R1, R15, R16: 10K0/S 1%; R0603
R3, R7: 3K3/S 1%; R0603
R4, R5, R6, R8: 1K/S 1%; R0603
SV1, SV2: MA10-2
U1, U2, U3, U4: MCP6G01T-E/OT; SOT95P300X145-5N
XT1: 10Mhz 8pf SMD 3,20x2,50; CTS_32X25

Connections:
+3V3: C3.1, C5.2, C10.1, C16.1, C17.1, C18.1, C19.1, IC1.28 (VDD), IC1.40 (VDD1), IC2.8 (VCC), ICSP.2, J2.1, J3.1, J4.1, J5.1, L1.2, R1.2, R3.1, R7.1, SV2.3, U1.5 (VDD), U2.5 (VDD), U3.5 (VDD), U4.5 (VDD); also elsewhere on the board
+5V: SV2.2; also elsewhere on the board
+12V: SV2.1; also elsewhere on the board
AP0: SV1.17, U3.3 (VIN+)
AP1: SV1.19, U4.3 (VIN+)
AP2: SV1.18, U1.3 (VIN+)
AP3: SV1.20, U2.3 (VIN+)
AVDD: C2.2, IC1.17 (AVDD), L1.1
CHA1: IC1.8 (PGED2/PWM1H3/RP10/CN16/PMD2/RB10), SV1.5
CHA2: IC1.42 (PGEC3/ASCL1/RP6/CN24/PMD6/RB6), SV1.6
CHB1: IC1.9 (PGEC2/PWM1L3/RP11/CN15/PMD1/RB11), SV1.7
CHB2: IC1.41 (PGED3/ASDA1/RP5/CN27/PMD7/RB5), SV1.8
EN1: IC1.13 (TCK/PMA7/RA7), SV1.13
EN2: IC1.12 (TMS/PMA10/RA10), SV1.14
GAIN_A1: J4.2, U3.4 (GSEL)
GAIN_ANA2: J2.2, U1.4 (GSEL)
GAIN_ANB2: J3.2, U2.4 (GSEL)
GAIN_B1: J5.2, U4.4 (GSEL)
GND: C1.2, C2.1, C3.2, C5.1, C6.2, C7.1, C10.2, C16.2, C17.2, C18.2, C19.2, IC1.6 (VSS), IC1.16 (AVSS), IC1.29 (VSS1), IC1.39 (VSS2), IC2.1 (A0), IC2.2 (A1), IC2.3 (A2), IC2.4 (GND), IC2.7 (WP), ICSP.3, J2.3, J3.3, J4.3, J5.3, J6.3, J7.3, LED1.C, LED2.C, LED3.C, LED4.C, SV1.15, SV1.16, SV2.4, SV2.9, SV2.10, SV2.19, U1.2 (VSS), U2.2 (VSS), U3.2 (VSS), U4.2 (VSS), XT1.2 (GND), XT1.4 (GND); also elsewhere on the board
GP0: IC1.35 (TDI/PMA9/RA9), SV2.12
GP1: IC1.25 (AN6/RP16/CN8/RC0), SV2.14
GP2: IC1.26 (AN7/RP17/CN9/RC1), SV2.16
GP3: IC1.27 (AN8/CVREF/RP18/PMA2/CN10/RC2), J4.4, SV2.18
GP4: IC1.36 (RP19/CN28/PMBE/RC3), J5.4, SV2.20
GP5: IC1.34 (SOSCO/T1CK/CN0/RA4), J3.4, SV2.17
GP6: IC1.33 (SOSCI/RP4/CN1/RB4), J2.4, SV2.15
GP7: IC1.43 (INT0/RP7/CN23/PMD5/RB7), J6.1
GP8: IC1.32 (TDO/PMA8/RA8), J7.1
LD1: IC1.2 (PWM2H1/RP22/CN18/PMA1/RC6), R4.1
LD2: IC1.3 (PWM2L1/RP23/CN17/PMA0/RC7), R5.1
LD3: IC1.4 (RP24/CN20/PMA5/RC8), R6.1
LD4: IC1.5 (RP25/CN19/PMA6/RC9), R8.1
MCLR: IC1.18 (MCLR), ICSP.1, R1.1
MCU_AP0: IC1.19 (AN0/VREF+/CN2/RA0), U3.1 (VOUT)
MCU_AP1: IC1.20 (AN1/VREF-/CN3/RA1), U4.1 (VOUT)
MCU_AP2/PGD: IC1.21 (PGED1/AN2/C2IN-/RP0/CN4/RB0), ICSP.4, R15.1
MCU_AP3/PGC: IC1.22 (PGEC1/AN3/C2IN+/RP1/CN5/RB1), ICSP.5, R16.1
unnamed: C7.2, IC1.30 (OSC1/CLKI/CN30/RA2), XT1.1 (X1)
unnamed: C6.1, IC1.31 (OSC2/CLKO/CN29/RA3), XT1.3 (X2)
unnamed: J6.2, SV1.2
unnamed: LED1.A, R4.2
unnamed: LED2.A, R5.2
unnamed: R15.2, U1.1 (VOUT)
unnamed: R16.2, U2.1 (VOUT)
unnamed: J7.2, SV1.1
PWMA1: IC1.14 (PWM1H1/RTCC/RP14/CN12/PMWR/RB14), SV1.9
PWMA2: IC1.10 (PWM1H2/DAC1RP/RP12/CN14/PMD0/RB12), SV1.10
PWMB1: IC1.15 (PWM1L1/RP15/CN11/PMCS1/RB15), SV1.11
PWMB2: IC1.11 (PWM1L2/DAC1RN/RP13/CN13/PMRD/RB13), SV1.12
RX1: IC1.38 (RP21/CN26/PMA3/RC5), SV2.7
RX2: IC1.24 (AN5/C1IN+/RP3/CN7/RB3), SV2.11
SCL: IC1.44 (SCL1/RP8/CN22/PMD4/RB8), IC2.6 (SCL), R3.2, SV2.8
SDA: IC1.1 (SDA1/RP9/CN21/PMD3/RB9), IC2.5 (SDA), R7.2, SV2.6
TX1: IC1.37 (RP20/CN25/PMA4/RC4), SV2.5
TX2: IC1.23 (AN4/C1IN-/RP2/CN6/RB2), SV2.13
VCAP/VDDCORE: C1.1, IC1.7 (VCAP/VDDCORE)
VENC: SV1.3, SV1.4; also elsewhere on the board
VENC1-LD3: LED3.A, R6.2
VENC2-LD4: LED4.A, R8.2

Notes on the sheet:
IO7 and IO8 can be used as Z channel of encoder
GPx : General porpouse Digital & Analog Input/Output pin
APx : Analog Input pin

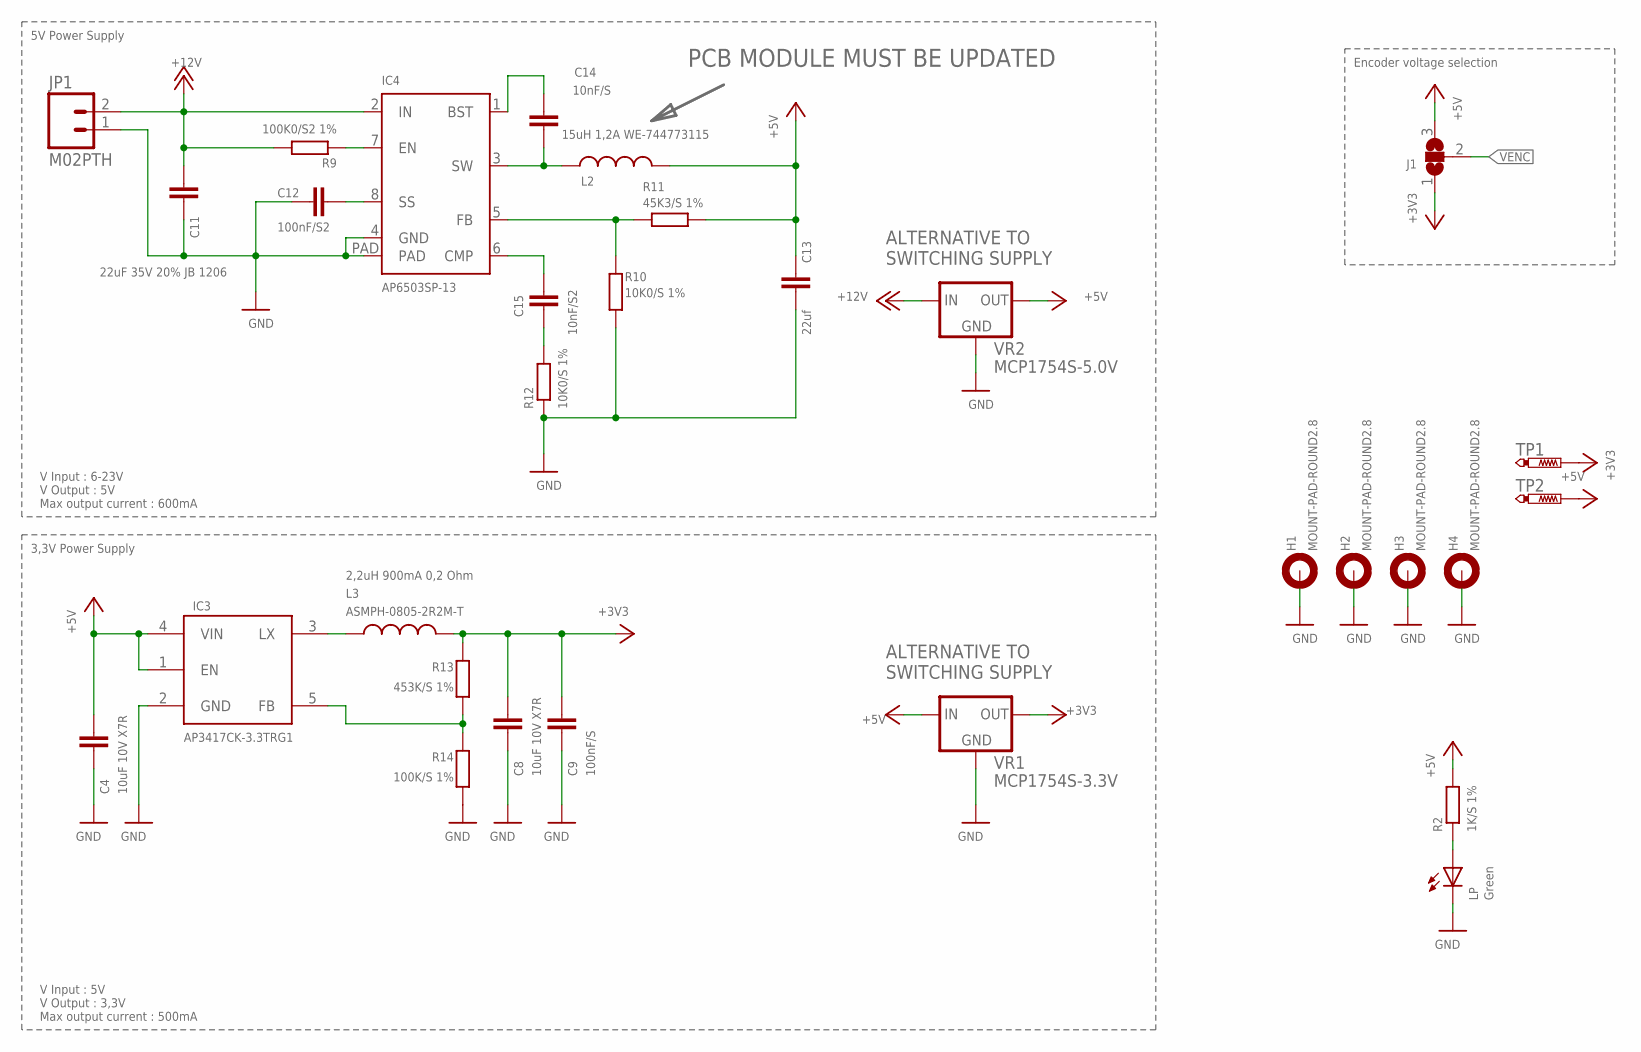
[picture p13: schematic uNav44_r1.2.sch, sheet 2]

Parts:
C4, C8: 10uF 10V X7R; C0805
C9: 100nF/S; C0603
C11: 22uF 35V 20% JB 1206; C1206
C12: 100nF/S2; C0603
C13: 22uf; C1206
C14: 10nF/S; C0603
C15: 10nF/S2; C0603
H1, H2, H3, H4: MOUNT-PAD-ROUND2.8; 2,8-PAD
IC3: AP3417CK-3.3TRG1; SOT-23-5
IC4: AP6503SP-13; SO-8EP
J1: SJ2W; SJ_2
JP1: M02PTH; 1X02
L2: 15uH 1,2A WE-744773115; 1210
L3: ASMPH-0805-2R2M-T; 0805
LP: Green; CHIPLED_0805
R2: 1K/S 1%; R0603
R9: 100K0/S2 1%; R0603
R10, R12: 10K0/S 1%; R0603
R11: 45K3/S 1%; R0603
R13: 453K/S 1%; R0603
R14: 100K/S 1%; R0603
TP1, TP2: PTR1TP07R; TP07R
VR1: MCP1754S-3.3V; SOT89
VR2: MCP1754S-5.0V; SOT89

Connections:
+3V3: C8.1, C9.1, J1.1, L3.2, R13.2, TP1.TP, VR1.3 (OUT); also elsewhere on the board
+5V: C4.1, C13.1, IC3.1 (EN), IC3.4 (VIN), J1.3, L2.2, R2.2, R11.2, TP2.TP, VR1.1 (IN), VR2.3 (OUT); also elsewhere on the board
+12V: C11.1, IC4.2 (IN), JP1.2, R9.2, VR2.1 (IN); also elsewhere on the board
GND: C4.2, C8.2, C9.2, C11.2, C12.2, C13.2, H1.B2,8, H2.B2,8, H3.B2,8, H4.B2,8, IC3.2 (GND), IC4.4 (GND), IC4.PAD, JP1.1, LP.C, R10.2, R12.1, R14.1, VR1.2 (GND), VR1.4 (GND), VR2.2 (GND), VR2.4 (GND); also elsewhere on the board
unnamed: IC3.3 (LX), L3.1
unnamed: C14.1, IC4.1 (BST)
unnamed: LP.A, R2.1
unnamed: IC4.7 (EN), R9.1
unnamed: IC3.5 (FB), R13.1, R14.2
unnamed: C12.1, IC4.8 (SS)
unnamed: IC4.5 (FB), R10.1, R11.1
unnamed: C14.2, IC4.3 (SW), L2.1
unnamed: C15.1, IC4.6 (CMP)
unnamed: C15.2, R12.2
VENC: J1.2; also elsewhere on the board

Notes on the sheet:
2,2uH 900mA 0,2 Ohm
Encoder voltage selection
5V Power Supply
V Input : 6-23V V Output : 5V Max output current : 600mA
3,3V Power Supply
V Input : 5V V Output : 3,3V Max output current : 500mA
ALTERNATIVE TO SWITCHING SUPPLY
PCB MODULE MUST BE UPDATED

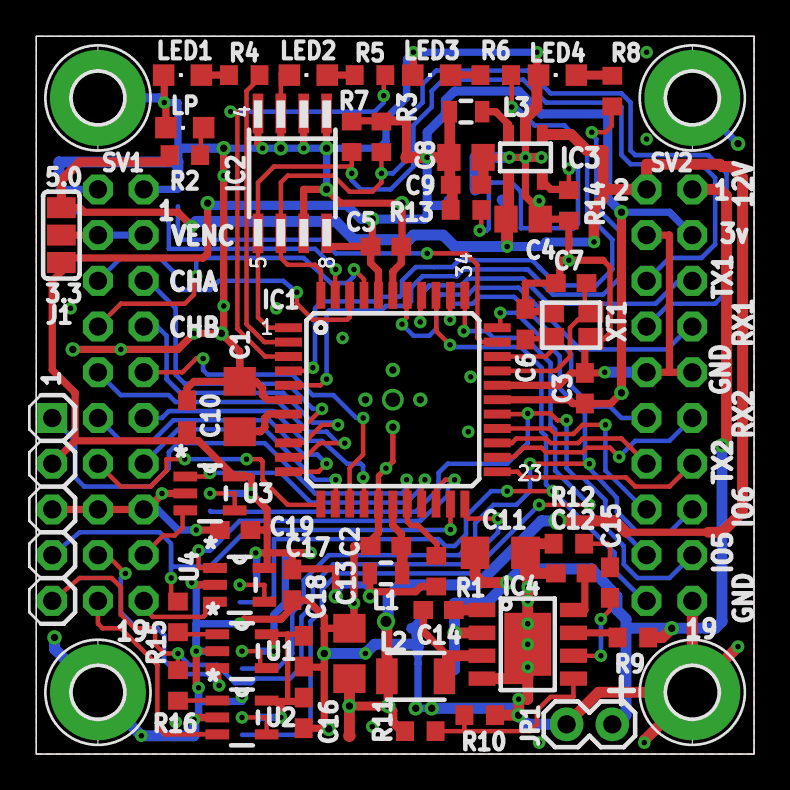
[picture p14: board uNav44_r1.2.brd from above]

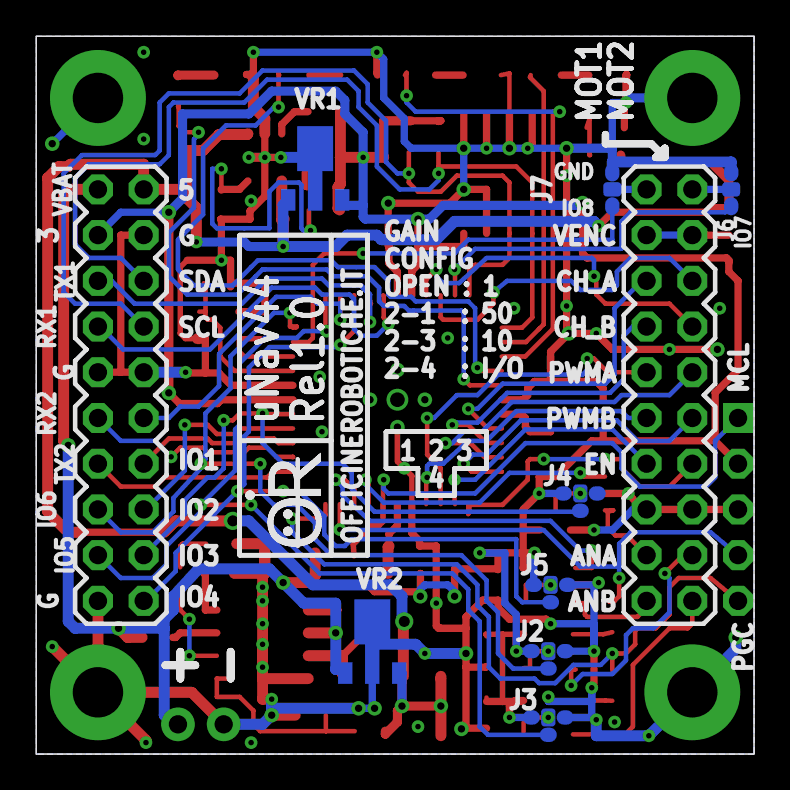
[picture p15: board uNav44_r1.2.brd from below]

Board: 2 copper layers, 39.9 x 39.9 mm, 71 parts (10 on the bottom side), 69 nets.

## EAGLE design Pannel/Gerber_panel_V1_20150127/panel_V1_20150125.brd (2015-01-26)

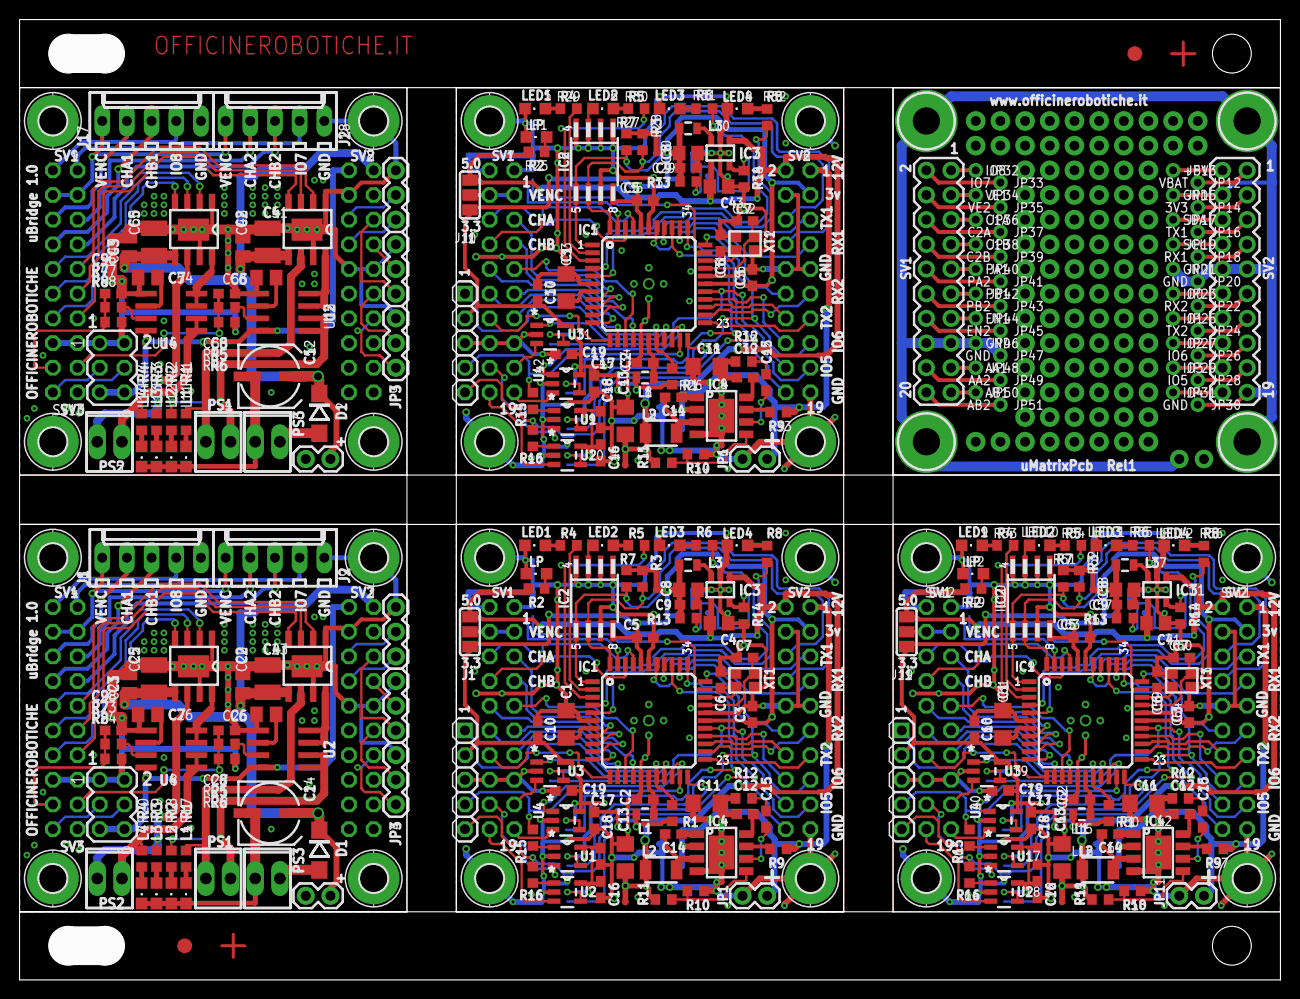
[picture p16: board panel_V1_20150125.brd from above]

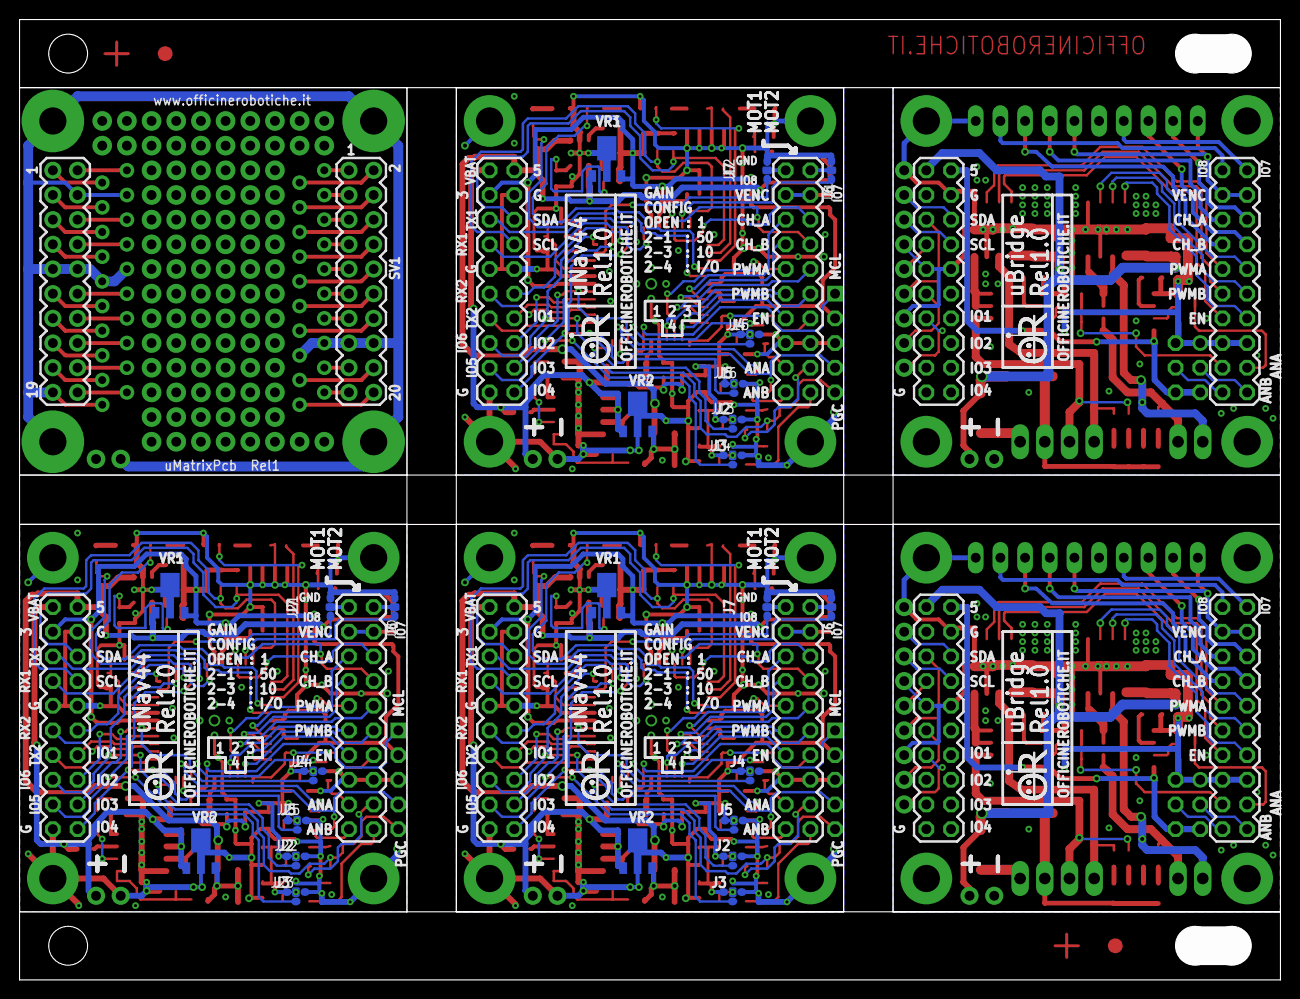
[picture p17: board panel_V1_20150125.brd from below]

Board: 2 copper layers, 129.8 x 98.9 mm, 338 parts (34 on the bottom side), 324 nets.

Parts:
C1, C33, C61: 10uf; C1206
C2, C3, C5, C9, C10, C16, C17, C18, C19, C29, C34, C35, C36, C37, C44, C45, C46, C47, C57, C62, C63, C64, C65, C72, C73, C74, C75: 100nF/S; C0603
C4, C8, C30, C43, C58, C71: 10uF 10V X7R; C0805
C6, C7, C31, C32, C59, C60: 18pf; C0603
C11, C38, C66: 22uF 35V 20% JB 1206; C1206
C12, C27, C28, C39, C55, C56, C67: 100nF/S2; C0603
C13, C40, C68: 22uf; C1206
C14, C41, C69: 10nF/S; C0603
C15, C42, C70: 10nF/S2; C0603
C20, C21, C48, C49: 220nF; C0805K
C22, C23, C50, C51: 10uF/S6 50V; C3225
C24, C52: PCE4554CT-ND; UD-6,3X7,7_NICHICON
C25, C26, C53, C54: 1nF; C0805K
D1, D2: ES1G-E2; DO214BA
H1, H2, H3, H4, H5, H6, H7, H8, H9, H10, H11, H12, H13, H14, H15, H16, H17, H18, H19, H20: MOUNT-PAD-ROUND2.8; 2,8-PAD
IC1, IC5, IC9: DSPIC33FJ128MC; TQFP44
IC2, IC6, IC10: 24LC024; SO-08M
IC3, IC7, IC11: AP3417CK-3.3TRG1; SOT-23-5
IC4, IC8, IC12: AP6503SP-13; SO-8EP
ICSP, ICSP1, ICSP2: 1X05-S
J1, J10, J19: SJ_2
J2, J3, J4, J5, J13, J14, J15, J16, J22, J23, J24, J25: C0R-JUMP-4
J6, J7, J11, J12, J20, J21: 0R-JUMPC; C0R-JMP
J8, J9, J17, J18: 22-27-2051-05; 6410-05
JP1, JP2, JP6, JP7, JP11: M02PTH; 1X02
JP3, JP4, JP5, JP8, JP9, JP10: 1X03
JP12, JP13, JP14, JP15, JP16, JP17, JP18, JP19, JP20, JP21, JP22, JP23, JP24, JP25, JP26, JP27, JP28, JP29, JP30, JP31, JP32, JP33, JP34, JP35, JP36, JP37, JP38, JP39, JP40, JP41, JP42, JP43, JP44, JP45, JP46, JP47, JP48, JP49, JP50, JP51: M01PTH_1.27MM_TESTPOINT; 1X0.127_TESTPOINT
L1, L8, L15: 22 uH; 0805
L2, L9, L16: 10uH_520mA; 1210
L3, L10, L17: ASMPH-0805-2R2M-T; 0805
L4, L6, L11, L13: LED0805-YEL/S; CHIPLED_0805
L5, L7, L12, L14: LED0805-GRN/S; CHIPLED_0805
LED1, LED2, LED5, LED6, LED9, LED10: LED0805-GRN/S; CHIPLED_0805
LED3, LED7, LED11: LED0805-YEL/S; CHIPLED_0805
LED4, LED8, LED12: LED0805-RED/S; CHIPLED_0805
LP, LP1, LP2: Green; CHIPLED_0805
PS1, PS2, PS3, PS4, PS5, PS6: 2POL254
R1, R10, R12, R15, R16, R26, R34, R36, R39, R40, R50, R58, R60, R63, R64: 10K0/S 1%; R0603
R2, R4, R5, R6, R8, R17, R18, R19, R20, R25, R29, R30, R31, R32, R41, R42, R43, R44, R49, R53, R54, R55, R56: 1K/S 1%; R0603
R3, R7, R22, R24, R27, R28, R46, R48, R51, R52: 3K3/S 1%; R0603
R9, R33, R57: 100K0/S2 1%; R0603
R11, R35, R59: 45K3/S 1%; R0603
R13, R37, R61: 450K/S 1%; R0603
R14, R38, R62: 100K/S 1%; R0603
R21, R23, R45, R47: 6K49/S 1%; R0603
SV1, SV2, SV3, SV4, SV6, SV7, SV8, SV9, SV11, SV12: MA10-2
SV5, SV10: MA03-2
TP1, TP2, TP3, TP4, TP5, TP6: PTR1TP07R; TP07R
U1, U2, U3, U4, U9, U10, U11, U12, U17, U18, U19, U20: MCP6G01T-E/OT; SOT95P300X145-5N
U5, U6, U13, U14: A4950; 8SOICN
U7, U8, U15, U16: ACS723; SO08
UN1: UNAV_BOARD
VR1, VR3, VR5: MCP1754S-3.3V; SOT89
VR2, VR4, VR6: MCP1754S-5.0V; SOT89
XT1, XT2, XT3: CTS_32X25

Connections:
+3V2: C29.1, C30.1, C35.2, C36.1, C37.1, C44.1, C45.1, C46.1, C47.1, IC5.28, IC5.40, IC6.8, ICSP1.2, J10.1, J13.1, J14.1, J15.1, J16.1, L8.2, L10.2, R26.2, R27.1, R28.1, R37.2, SV6.3, TP3.TP, U9.5, U10.5, U11.5, U12.5, VR3.3
+3V3: C3.1, C5.2, C8.1, C9.1, C10.1, C16.1, C17.1, C18.1, C19.1, IC1.28, IC1.40, IC2.8, ICSP.2, J1.1, J2.1, J3.1, J4.1, J5.1, L1.2, L3.2, R1.2, R3.1, R7.1, R13.2, SV2.3, TP1.TP, U1.5, U2.5, U3.5, U4.5, VR1.3
+3V5: C57.1, C58.1, C63.2, C64.1, C65.1, C72.1, C73.1, C74.1, C75.1, IC9.28, IC9.40, IC10.8, ICSP2.2, J19.1, J22.1, J23.1, J24.1, J25.1, L15.2, L17.2, R50.2, R51.1, R52.1, R61.2, SV11.3, TP5.TP, U17.5, U18.5, U19.5, U20.5, VR5.3
+3V6: JP14.1, UN1.+3V3
+5V: C4.1, C13.1, IC3.1, IC3.4, J1.3, L2.2, R2.2, R11.2, SV2.2, TP2.TP, VR1.1, VR2.3
+5V1: SV3.2, SV5.5, SV5.6, U7.8, U8.8
+5V2: C40.1, C43.1, IC7.1, IC7.4, J10.3, L9.2, R25.2, R35.2, SV6.2, TP4.TP, VR3.1, VR4.3
+5V3: SV8.2, SV10.5, SV10.6, U15.8, U16.8
+5V4: C68.1, C71.1, IC11.1, IC11.4, J19.3, L16.2, R49.2, R59.2, SV11.2, TP6.TP, VR5.1, VR6.3
+5V5: JP13.1, UN1.+5V
+12V: C11.1, IC4.2, JP1.2, R9.2, SV2.1, VR2.1
+12V1: C20.2, C21.2, C22.2, C23.2, C24.+, D1.C, JP2.2, SV3.1, U5.5, U6.5
+12V2: C38.1, IC8.2, JP6.2, R33.2, SV6.1, VR4.1
+12V3: C48.2, C49.2, C50.2, C51.2, C52.+, D2.C, JP7.2, SV8.1, U13.5, U14.5
+12V4: C66.1, IC12.2, JP11.2, R57.2, SV11.1, VR6.1
+12V5: JP12.1, UN1.VBAT
ANA1: IC1.19, U3.1
ANA2: SV1.18, U1.3
ANA2/PGD: IC1.21, ICSP.4, R15.1
ANA2/PGD1: IC5.21, ICSP1.4, R39.1
ANA2/PGD2: IC9.21, ICSP2.4, R63.1
ANA3: C27.1, R21.1, R22.2, SV4.17
ANA4: C28.1, R23.1, R24.2, SV4.18
ANA5: IC5.19, U11.1
ANA6: SV7.18, U9.3
ANA7: C55.1, R45.1, R46.2, SV9.17
ANA8: C56.1, R47.1, R48.2, SV9.18
ANA9: IC9.19, U19.1
ANA10: SV12.18, U17.3
ANA11: JP49.1, UN1.ANA2
ANB1: IC1.20, U4.1
ANB2: SV1.20, U2.3
ANB2/PGC: IC1.22, ICSP.5, R16.1
ANB2/PGC1: IC5.22, ICSP1.5, R40.1
ANB2/PGC2: IC9.22, ICSP2.5, R64.1
ANB3: SV4.19, SV5.4
ANB4: SV4.20, SV5.3
ANB5: IC5.20, U12.1
ANB6: SV7.20, U10.3
ANB7: SV9.19, SV10.4
ANB8: SV9.20, SV10.3
ANB9: IC9.20, U20.1
ANB10: SV12.20, U18.3
ANB11: JP51.1, UN1.ANB2
AVDD: C2.2, IC1.17, L1.1
AVDD1: C34.2, IC5.17, L8.1
AVDD2: C62.2, IC9.17, L15.1
CHA1: IC1.8, SV1.5
CHA2: IC1.42, SV1.6
CHA3: J9.4, SV4.5
CHA4: J8.4, SV4.6
CHA5: IC5.8, SV7.5
CHA6: IC5.42, SV7.6
CHA7: J18.4, SV9.5
CHA8: J17.4, SV9.6
CHA9: IC9.8, SV12.5
CHA10: IC9.42, SV12.6
CHA11: JP36.1, UN1.CH1A
CHA12: JP37.1, UN1.CH2A
CHB1: IC1.9, SV1.7
CHB2: IC1.41, SV1.8
CHB3: J9.3, SV4.7
CHB4: J8.3, SV4.8
CHB5: IC5.9, SV7.7
CHB6: IC5.41, SV7.8
CHB7: J18.3, SV9.7
CHB8: J17.3, SV9.8
CHB9: IC9.9, SV12.7
CHB10: IC9.41, SV12.8
CHB11: JP38.1, UN1.CH1B
CHB12: JP39.1, UN1.CH2B
EN1: IC1.13, SV1.13
EN2: IC1.12, SV1.14
EN3: SV4.13, U5.4
EN4: SV4.14, U6.4
EN5: IC5.13, SV7.13
EN6: IC5.12, SV7.14
EN7: SV9.13, U13.4
EN8: SV9.14, U14.4
EN9: IC9.13, SV12.13
EN10: IC9.12, SV12.14
EN11: JP44.1, UN1.EN1
EN12: JP45.1, UN1.EN2
GAIN_A1: J4.2, U3.4
GAIN_A2: J15.2, U11.4
GAIN_A3: J24.2, U19.4
GAIN_ANA1: J13.2, U9.4
GAIN_ANA2: J2.2, U1.4
GAIN_ANA3: J22.2, U17.4
GAIN_ANB1: J14.2, U10.4
GAIN_ANB2: J3.2, U2.4
GAIN_ANB3: J23.2, U18.4
GAIN_B1: J5.2, U4.4
GAIN_B2: J16.2, U12.4
GAIN_B3: J25.2, U20.4
GND: C1.2, C2.1, C3.2, C4.2, C5.1, C6.2, C7.1, C8.2, C9.2, C10.2, C11.2, C12.2, C13.2, C16.2, C17.2, C18.2, C19.2, H1.B2,8, H2.B2,8, H3.B2,8, H4.B2,8, IC1.6, IC1.16, IC1.29, IC1.39, IC2.1, IC2.2, IC2.3, IC2.4, IC2.7, IC3.2, IC4.4, IC4.PAD, ICSP.3, J2.3, J3.3, J4.3, J5.3, J6.3, J7.3, JP1.1, LED1.C, LED2.C, LED3.C, LED4.C, LP.C, R10.2, R12.1, R14.1, SV1.15, SV1.16, SV2.4, SV2.9, SV2.10, SV2.19, U1.2, U2.2, U3.2, U4.2, VR1.2, VR1.4, VR2.2, VR2.4, XT1.2, XT1.4
GND1: C20.1, C21.1, C22.1, C23.1, C24.-, C25.2, C26.2, C27.2, C28.2, H5.B2,8, H6.B2,8, H7.B2,8, H8.B2,8, J8.1, J9.1, JP2.1, JP3.3, JP4.3, JP5.3, L4.C, L5.C, L6.C, L7.C, PS3.1, R22.1, R24.1, SV3.4, SV3.9, SV3.10, SV3.19, SV4.15, SV4.16, SV5.1, SV5.2, U5.1, U5.7, U5.PAD, U6.1, U6.7, U6.PAD, U7.5, U8.5
GND2: C29.2, C30.2, C31.2, C32.1, C33.2, C34.1, C35.1, C36.2, C37.2, C38.2, C39.2, C40.2, C43.2, C44.2, C45.2, C46.2, C47.2, H9.B2,8, H10.B2,8, H11.B2,8, H12.B2,8, IC5.6, IC5.16, IC5.29, IC5.39, IC6.1, IC6.2, IC6.3, IC6.4, IC6.7, IC7.2, IC8.4, IC8.PAD, ICSP1.3, J11.3, J12.3, J13.3, J14.3, J15.3, J16.3, JP6.1, LED5.C, LED6.C, LED7.C, LED8.C, LP1.C, R34.2, R36.1, R38.1, SV6.4, SV6.9, SV6.10, SV6.19, SV7.15, SV7.16, U9.2, U10.2, U11.2, U12.2, VR3.2, VR3.4, VR4.2, VR4.4, XT2.2, XT2.4
GND3: C48.1, C49.1, C50.1, C51.1, C52.-, C53.2, C54.2, C55.2, C56.2, H13.B2,8, H14.B2,8, H15.B2,8, H16.B2,8, J17.1, J18.1, JP7.1, JP8.3, JP9.3, JP10.3, L11.C, L12.C, L13.C, L14.C, PS6.1, R46.1, R48.1, SV8.4, SV8.9, SV8.10, SV8.19, SV9.15, SV9.16, SV10.1, SV10.2, U13.1, U13.7, U13.PAD, U14.1, U14.7, U14.PAD, U15.5, U16.5
GND4: C57.2, C58.2, C59.2, C60.1, C61.2, C62.1, C63.1, C64.2, C65.2, C66.2, C67.2, C68.2, C71.2, C72.2, C73.2, C74.2, C75.2, H17.B2,8, H18.B2,8, H19.B2,8, H20.B2,8, IC9.6, IC9.16, IC9.29, IC9.39, IC10.1, IC10.2, IC10.3, IC10.4, IC10.7, IC11.2, IC12.4, IC12.PAD, ICSP2.3, J20.3, J21.3, J22.3, J23.3, J24.3, J25.3, JP11.1, LED9.C, LED10.C, LED11.C, LED12.C, LP2.C, R58.2, R60.1, R62.1, SV11.4, SV11.9, SV11.10, SV11.19, SV12.15, SV12.16, U17.2, U18.2, U19.2, U20.2, VR5.2, VR5.4, VR6.2, VR6.4, XT3.2, XT3.4
GND6: JP15.1, JP20.1, JP21.1, JP30.1, JP46.1, JP47.1, UN1.GND@1, UN1.GND@2, UN1.GND@3, UN1.GND@4, UN1.GND@5, UN1.GND@6, UN1.H1, UN1.H2, UN1.H3, UN1.H4, UN1.P_GND
IN_A1: SV1.17, U3.3
IN_A2: SV7.17, U11.3
IN_A3: SV12.17, U19.3
IN_A4: JP48.1, UN1.ANA1
IN_B1: SV1.19, U4.3
IN_B2: SV7.19, U12.3
IN_B3: SV12.19, U20.3
IN_B5: JP50.1, UN1.ANB1
IO0: IC1.35, SV2.12
IO1: IC1.25, SV2.14
IO2: IC1.26, SV2.16
IO3: IC1.27, J4.4, SV2.18
IO4: IC1.36, J5.4, SV2.20
IO5: IC1.34, J3.4, SV2.17
IO6: IC1.33, J2.4, SV2.15
IO7: IC1.43, J6.1
IO8: IC1.32, J7.1
IO9: J9.2, SV4.1
IO10: J8.2, SV4.2
IO18: IC5.32, J12.1
IO19: IC5.43, J11.1
IO20: IC5.36, J16.4, SV6.20
IO21: IC5.27, J15.4, SV6.18
IO22: IC5.26, SV6.16
IO23: IC5.25, SV6.14
IO24: IC5.34, J14.4, SV6.17
IO25: IC5.33, J13.4, SV6.15
IO26: IC5.35, SV6.12
IO27: J18.2, SV9.1
IO28: J17.2, SV9.2
IO36: IC9.32, J21.1
IO37: IC9.43, J20.1
IO38: IC9.36, J25.4, SV11.20
IO39: IC9.27, J24.4, SV11.18
IO40: IC9.26, SV11.16
IO41: IC9.25, SV11.14
IO42: IC9.34, J23.4, SV11.17
IO43: IC9.33, J22.4, SV11.15
IO44: IC9.35, SV11.12
IO45: JP23.1, UN1.IO0
IO46: JP25.1, UN1.IO1
IO47: JP26.1, UN1.IO6
IO48: JP27.1, UN1.IO2
IO49: JP28.1, UN1.IO5
IO50: JP29.1, UN1.IO3
IO51: JP31.1, UN1.IO4
IO52: JP32.1, UN1.IO8
IO54: JP33.1, UN1.IO7
LD1: IC1.2, R4.1
LD2: IC1.3, R5.1
LD3: IC1.4, R6.1
LD4: IC1.5, R8.1
LD5: IC5.3, R30.1
LD6: IC5.2, R29.1
LD7: IC5.5, R32.1
LD8: IC5.4, R31.1
LD9: IC9.3, R54.1
LD10: IC9.2, R53.1
LD11: IC9.5, R56.1
LD12: IC9.4, R55.1
MCLR: IC1.18, ICSP.1, R1.1
MCLR1: IC5.18, ICSP1.1, R26.1
MCLR2: IC9.18, ICSP2.1, R50.1
unnamed: IC3.3, L3.1
unnamed: C7.2, IC1.30, XT1.1
unnamed: C6.1, IC1.31, XT1.3
unnamed: C14.1, IC4.1
unnamed: LP.A, R2.1
unnamed: IC4.7, R9.1
unnamed: IC3.5, R13.1, R14.2
unnamed: C12.1, IC4.8
unnamed: IC4.5, R10.1, R11.1
unnamed: J6.2, SV1.2
unnamed: L4.A, R17.2
unnamed: LED1.A, R4.2
unnamed: LED2.A, R5.2
unnamed: L5.A, R18.2
unnamed: C14.2, IC4.3, L2.1
unnamed: C15.1, IC4.6
unnamed: C15.2, R12.2
unnamed: U5.8, U7.3, U7.4
unnamed: U6.8, U8.3, U8.4
unnamed: PS1.2, R18.1, U7.1, U7.2
unnamed: R15.2, U1.1
unnamed: R16.2, U2.1
unnamed: J7.2, SV1.1
unnamed: PS2.2, R20.1, U8.1, U8.2
unnamed: PS1.1, R17.1, U5.6
unnamed: PS2.1, R19.1, U6.6
unnamed: C25.1, U7.6
unnamed: C26.1, U8.6
unnamed: R21.2, U7.7
unnamed: R23.2, U8.7
unnamed: D1.A, PS3.2
unnamed: C32.2, IC5.30, XT2.1
unnamed: C31.1, IC5.31, XT2.3
unnamed: LED5.A, R29.2
unnamed: LED6.A, R30.2
unnamed: LP1.A, R25.1
unnamed: IC8.7, R33.1
unnamed: C39.1, IC8.8
unnamed: IC8.5, R34.1, R35.1
unnamed: C41.2, IC8.3, L9.1
unnamed: C42.1, IC8.6
unnamed: C42.2, R36.2
unnamed: C41.1, IC8.1
unnamed: IC7.3, L10.1
unnamed: IC7.5, R37.1, R38.2
unnamed: R39.2, U9.1
unnamed: R40.2, U10.1
unnamed: J11.2, SV7.2
unnamed: J12.2, SV7.1
unnamed: L11.A, R41.2
unnamed: L12.A, R42.2
unnamed: U13.8, U15.3, U15.4
unnamed: U14.8, U16.3, U16.4
unnamed: PS4.2, R42.1, U15.1, U15.2
unnamed: PS5.2, R44.1, U16.1, U16.2
unnamed: PS4.1, R41.1, U13.6
unnamed: PS5.1, R43.1, U14.6
unnamed: C53.1, U15.6
unnamed: C54.1, U16.6
unnamed: R45.2, U15.7
unnamed: R47.2, U16.7
unnamed: D2.A, PS6.2
unnamed: C60.2, IC9.30, XT3.1
unnamed: C59.1, IC9.31, XT3.3
unnamed: LED9.A, R53.2
unnamed: LED10.A, R54.2
unnamed: LP2.A, R49.1
unnamed: IC12.7, R57.1
unnamed: C67.1, IC12.8
unnamed: IC12.5, R58.1, R59.1
unnamed: C69.2, IC12.3, L16.1
unnamed: C70.1, IC12.6
unnamed: C70.2, R60.2
unnamed: C69.1, IC12.1
unnamed: IC11.3, L17.1
unnamed: IC11.5, R61.1, R62.2
unnamed: R63.2, U17.1
unnamed: R64.2, U18.1
unnamed: J20.2, SV12.2
unnamed: J21.2, SV12.1
PWMA1: IC1.14, SV1.9
PWMA2: IC1.10, SV1.10
PWMA3: SV4.9, U5.2
PWMA4: SV4.10, U6.2
PWMA5: IC5.14, SV7.9
PWMA6: IC5.10, SV7.10
PWMA7: SV9.9, U13.2
PWMA8: SV9.10, U14.2
PWMA9: IC9.14, SV12.9
PWMA10: IC9.10, SV12.10
PWMA11: JP40.1, UN1.PWMA1
PWMA12: JP41.1, UN1.PWMA2
PWMB1: IC1.15, SV1.11
PWMB2: IC1.11, SV1.12
PWMB3: SV4.11, U5.3
PWMB4: SV4.12, U6.3
PWMB5: IC5.15, SV7.11
PWMB6: IC5.11, SV7.12
PWMB7: SV9.11, U13.3
PWMB8: SV9.12, U14.3
PWMB9: IC9.15, SV12.11
PWMB10: IC9.11, SV12.12
PWMB11: JP42.1, UN1.PWMB1
PWMB12: JP43.1, UN1.PWMB2
RX1: IC1.38, SV2.7
RX2: IC1.24, SV2.11
RX3: JP4.2, SV3.11
RX4: JP3.2, SV3.7
RX5: IC5.24, SV6.11
RX6: IC5.38, SV6.7
RX7: JP9.2, SV8.11
RX8: JP8.2, SV8.7
RX9: IC9.24, SV11.11
RX10: IC9.38, SV11.7
RX11: JP18.1, UN1.RX1
RX12: JP22.1, UN1.RX2
SCL: IC1.44, IC2.6, R3.2, SV2.8
SCL1: JP5.1, SV3.8
SCL2: IC5.44, IC6.6, R28.2, SV6.8
SCL3: JP10.1, SV8.8
SCL4: IC9.44, IC10.6, R52.2, SV11.8
SCL5: JP19.1, UN1.SCL
SDA: IC1.1, IC2.5, R7.2, SV2.6
SDA1: JP5.2, SV3.6
SDA2: IC5.1, IC6.5, R27.2, SV6.6
SDA3: JP10.2, SV8.6
SDA4: IC9.1, IC10.5, R51.2, SV11.6
SDA5: JP17.1, UN1.SDA
TX1: IC1.37, SV2.5
TX2: IC1.23, SV2.13
TX3: JP3.1, SV3.5
TX4: JP4.1, SV3.13
TX5: IC5.37, SV6.5
TX6: IC5.23, SV6.13
TX7: JP8.1, SV8.5
TX8: JP9.1, SV8.13
TX9: IC9.37, SV11.5
TX10: IC9.23, SV11.13
TX11: JP16.1, UN1.TX1
TX13: JP24.1, UN1.TX2
VCAP/VDDCORE: C1.1, IC1.7
VCAP/VDDCORE1: C33.1, IC5.7
VCAP/VDDCORE2: C61.1, IC9.7
VENC: J1.2, SV1.3, SV1.4
VENC1: J8.5, J9.5, SV4.3, SV4.4
VENC1-LD1: L6.A, R19.2
VENC1-LD2: LED7.A, R31.2
VENC1-LD3: LED3.A, R6.2
VENC1-LD4: L13.A, R43.2
VENC1-LD5: LED11.A, R55.2
VENC2: J10.2, SV7.3, SV7.4
VENC2-LD1: L7.A, R20.2
VENC2-LD2: LED8.A, R32.2
VENC2-LD3: L14.A, R44.2
VENC2-LD4: LED4.A, R8.2
VENC2-LD5: LED12.A, R56.2
VENC3: J17.5, J18.5, SV9.3, SV9.4
VENC4: J19.2, SV12.3, SV12.4
VENC5: JP35.1, UN1.VENC@1
VENC6: JP34.1, UN1.VENC@2

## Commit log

2015-01-10 Add Vencoder voltage selection \ Removed connection of LED3 and LED4 from connector \ @katodo : PCB update is needed
    [uNav44_r1.brd, uNav44_r1.sch]
2015-01-11 Add filter on ACS / Update with ACS filter and GND top layer / @katodo i suggest to check files
    [uBridge44_r1.brd, uNav44_r1.brd]
2015-01-11 encoder connettor for motor / @katodo ready for you
    [uBridge44_r1.brd, uBridge44_r1.sch]
2015-01-13 useless files removed
    [Master10.brd, Master10.sch, MasterAlternativo10.brd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]
2015-01-14 Add 5 and 3.3V regulator / @katodo you must verify
    [uNav44_r1.brd, uNav44_r1.sch]
2015-01-14 Changed some component package to optimize space.
    [uNav44_r1.brd, uNav44_r1.sch]
2015-01-18 Scheme update with Operational Amplifier and switching supply
    [uNav44_r1.brd, uNav44_r1.sch]
2015-01-18 Work in progress... update image of layout
    [uNav44_r1.brd, uNav44_r1.sch]
2015-01-19 Re-Added LDO regulator as option for a LOW-COST version of board. Added jumper to fix IO7 & IO8 to GND to facilitate Encoder cabling in application without Z-Axis
    [uNav44_r1.brd, uNav44_r1.sch]
2015-01-20 With a new 4-via Jumper now OA gain can be controlled by MCU
    [uNav44_r1.brd, uNav44_r1.sch]
2015-01-22 First release with 100% routing complete... and some error :)
    [uNav44_r1.brd, uNav44_r1.sch]
2015-01-22 Update of some file
    [uNav44_r1.brd, uNav44_r1.sch]
2015-01-24 uNAV44 finished.
    [uNav44_r1.BottomCream.gbr, uNav44_r1.Layer_Bottom.gbr, uNav44_r1.Layer_Top.gbr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]
2015-01-25 Create PCB panellization and correct some issue on silkscreen
    [panel_V1_20150125.BottomCream.gbr, panel_V1_20150125.Layer_Bottom.gbr, panel_V1_20150125.Layer_Top.gbr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]
2015-01-26 Final release of PCB with a first version of partlist ( In OpenOffice Calc format )
    [panel_V1_20150125.BottomCream.gbr, panel_V1_20150125.Layer_Bottom.gbr, panel_V1_20150125.Layer_Top.gbr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]
2015-03-24 Little update on component value, Rlease 1.1 created.
    [uNav44_r1.1.brd, uNav44_r1.1.sch, uNav44_r1.ods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]
2015-08-10 Reviewed some pin name
    [uNav44_r1.2.brd, uNav44_r1.2.sch]

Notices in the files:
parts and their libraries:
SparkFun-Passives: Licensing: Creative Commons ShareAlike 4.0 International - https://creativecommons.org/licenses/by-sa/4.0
